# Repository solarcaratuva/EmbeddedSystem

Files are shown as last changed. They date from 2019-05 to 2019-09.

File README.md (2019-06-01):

# UVA Solar Car Team Electrical Team - Embedded System Subgroup
The embedded system sub-group focuses on developing the embedded system for the solar car that controls the CAN bus, driver interface and BPS (Battery Management System). This repository contains all of the design files necessary to implement the electrical control systems necessary for the Solar Car project.

## ECU
The ECU is the primary controller for the majority of systems, including motor control, battery monitoring, driver interface, and MPPT interface. The PCB contains circuitry for interfacing buttons and switches on driver interface, high-current lights and horn, as well as

**!important!**
Not all pins are 12V or even 5V compatible. Certain pins connect directly to the teensy with no protection.

* signal: name of IO signal in Eeschema (may or may not also be the net name)
* voltage: the voltages the pin is designed for
* direction: The direction of the signal relative to the ECU
* description: description of the signal

### User interface input (control)
These pins are used for allowing the driver to command the vehicle. All but the UART pins are 12V logic. To reduce the number of pins required on the MCU, we chose to wire 3 way position switches such that the end contacts connect to the rails and the center contact floats with a resistor divider to ensure the voltage is approximately VCC/2 when the switch is in the middle position.

| signal | pin  | voltage  | direction | description |
|:---:|:----:|:---:|:---:|:---:|
| BRAKE_CTRL |  20  | 0 - 12V  |  input | brake potentiometer, used to implement regen |
| REGEN_CTRL |  17  | 0 - 12V  |  input | regen potentiometer, used to set max regen percentage |
| GEARSHIFT_CTRL  |  14  | 0 - 12V  |  input | 3 way position switch. 12V = forward, 6V = neutral, 0V = reverse |
| TURNSIG_CTRL |  15  | 0 - 12V  |  input | 3 way position switch. 12V = forward, 6V = neutral, 0V = reverse |
| THROTTLE_CTRL |  16  | 0 - 12V  |  input | throttle potentiometer, the gas petal |
| STEER_CTRL |21(A7)| 0 - 12V  |  input | potentiometer on steering wheel, may be used for differential throttle control |
| HAZARD_CTRL |  16  | 0 - 12V  |  input | pushbutton used to activate hazard lights, toggles on changing edge  |
| HORN_CTRL |22(A6)| 0 - 12V  |  input | horn button |
| DOWN_CTRL |  26  | 0 - 12V  |  input | GUI navigation pushbutton |
| UP_CTRL |  27  | 0 - 12V  |  input | GUI navigation pushbutton |
| SEL_CTRL |  28  | 0 - 12V  |  input | GUI navigation pushbutton |
| KILL_SENSE | 2  | 0 - 12V  |  input | used to detect if the power engaging the relays has been cut |
| HAZARD_LED |  25  | 0 - 12V  |  output | connected to hazard button LED |
| UART_1_RX | 0  | 0 - 3.3V |  input | used for Nextion 3.2" LCD |
| UART_1_TX | 1  | 0 - 3.3V |  output | used for Nextion 3.2" LCD |

### Serial interface IO
These pins are used for communicating with various peripherals, components, and subsystems within the car. CAN0 is reserved for the BMS, while CAN1 is used for all less critical systems. UART pins are for future use.

| signal |  pin | voltage  | direction | description |
|:---:|:---:|:---:|:---:|:---:|
| CAN0_H | | 0 - 5V | CAN high  | connected to CAN0 peripheral on Teensy 3.6 through MCP2562 |
| CAN0_L | | 0 - 5V | CAN low | connected to CAN0 peripheral on Teensy 3.6 through MCP2562 |
| CAN1_H | | 0 - 5V | CAN high  | connected to CAN1 peripheral on Teensy 3.6 through MCP2562 |
| CAN1_L | | 0 - 5V | CAN low | connected to CAN1 peripheral on Teensy 3.6 through MCP2562 |
| UART_3_RX | 7 | 0 - 3.3V |  input | reserved for future use |
| UART_3_TX | 8 | 0 - 3.3V |  output | reserved for future use |
| UART_6_RX | 47 | 0 - 3.3V |  input | reserved for future use |
| UART_6_TX | 48 | 0 - 3.3V |  output | reserved for future use |

### Lights and Horn
These pins are capable of high currents (up to 5A distributed among the 4 outputs)

| signal | pin | voltage  | direction | description |
|:---:|:---:|:---:|:---:|:---:|
| HORN | 57 | 0 - 12V  | output  | high power output for car horn (can only source current) |
| HEADLIGHTS | 42 | 0 - 12V  | output  | high power output for headlights (can only source current) |
| BRAKELIGHTS | 56 | 0 - 12V  | output  | high power output for brakelights (can only source current) |
| STROBE | 6 | 0 - 12V  | output  | high power output for strobelight (can only source current) |
| RIGHT_BLINKERS  | 41 | 0 - 12V  | output  | high power output for right blinkers (can only source current) |
| LEFT_BLINKERS | 40 | 0 - 12V  | output  | high power output for left blinkers (can only source current) |
| HORN_CTRL | 22 | 0 - 12V  | input | high power input for horn |
| HEADLIGHT_CTRL  | 23 | 0 - 12V  | input | high power input for headlights |
| BRAKE_CTRL | 20 | 0 - 12v  | input | analog input for brakes (used for regen) |

### Motor control
The motor can be interfaced via UART, CAN, and GPIO. As of now, we do not have any API or knowledge of how to interface the motor over UART, as it is not documented. However it is possible to decompile the android app and reverse engineer whatever the app implements. For now, we are using CAN to retrieve important parameters from the motor such as voltage, current, RPM, throttle, and error codes. The motor only outputs messages over CAN, and does not interpret them.

The table below holds true for both `MOTOR_R*` and `MOTOR_L*` signals.
NOTE: all node names in the table below are preceded with `MOTOR_R*` and `MOTOR_L*`!

| signal | pin (L) | pin (R) |  voltage | direction | description |
|:---:|:---|:---:|:---:|:---:|:---:|
| REGEN_EN | 50 | 53 | 0 - 12V  | output  | enables regenerative braking on motor controller |
| REGEN | 36(pwm) | 37(pwm) | 0 - 5V | output  | analog output sets regen level when throttle is disabled (????) |
| THROTTLE | 35(pwm) | 38(pwm) | 0 - 5V | output  | sets throttle when FWD_EN or REV_EN are enabled. |
| ECO_EN | 49 | 39 | 0 - 12V  | output  | Reduces maximum power of motor controller |
| METER | A11 | A10 | 0 - 12V  | input | analog output from motor controller (????) |
| FWD_EN | 55 | 52 | 0 - 12V  | output  | forward enable |
| REV_EN | 54 | 51 | 0 - 12V  | output  | reverse enable |

## Software
At the moment we have bits and pieces of code written but no unified project as of yet. The CAN repository contains experemantal code for interfacing the CAN peripherals on the Teensy as well as development towards a motor driver. The completed motor driver will eventually be refactored into this repo.

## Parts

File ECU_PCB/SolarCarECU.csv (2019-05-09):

Id | Designator | Package | Quantity | Designation | Supplier and ref
1 | C41,C39,C21,C30,C35,C37,C38,C40 | C_0603_1608Metric | 8 | C
2 | R58,R59,R12,R13,R18,R19,R28,R29,R30,R31,R40,R41,R44,R45,R46,R47 | R_0603_1608Metric | 16 | R
3 | D6,D10,D9,D7,D5,D4,D8,D3 | D_SOD-123 | 8 | D
4 | U1 | Teensy35_36 | 1 | Teensy3.6
5 | R43 | R_1206_3216Metric | 1 | 0
6 | R53,R38,R52,R6,R32,R33,R34,R35,R36,R37,R39 | R_0603_1608Metric | 11 | 1k
7 | U4 | PT78NR112H | 1 | L7805
8 | C28,C26,C27,C29 | C_0603_1608Metric | 4 | 6.8n
9 | U8,U7,U9 | SOIC-16_3.9x9.9mm_P1.27mm | 3 | 4504
10 | BT1 | BatteryHolder_Keystone_1060_1x2032 | 1 | Battery_Cell
11 | J2 | USB_B_OST_USB-B1HSxx_Horizontal | 1 | USB_B
12 | R54,R55,R56,R57,R5,R42 | R_0603_1608Metric | 6 | 47
13 | C3,C2,C11,C12,C13,C14,C15,C16,C17,C36 | C_0603_1608Metric | 10 | 0.47u
14 | C8,C7 | C_0603_1608Metric | 2 | 47u
15 | R48,R49,R50,R51 | R_0603_1608Metric | 4 | 4.7
16 | U10 | SOIC-14_3.9x8.7mm_P1.27mm | 1 | LM324A
17 | C1,C4 | CP_Radial_D13.0mm_P5.00mm | 2 | 470uF
18 | C5,C6,C18,C19,C20 | C_0603_1608Metric | 5 | 4.7u
19 | C9 | C_0603_1608Metric | 1 | 10uF
20 | C10 | CP_Radial_D13.0mm_P5.00mm | 1 | 10uF
21 | C22,C23,C24,C25 | C_0603_1608Metric | 4 | 3.3n
22 | C31,C32,C33,C34 | C_0603_1608Metric | 4 | 2.2n
23 | J4,J5 | PinSocket_1x08_P2.54mm_Vertical | 2 | Screw_Terminal_01x08
24 | J6,J7 | PinSocket_1x14_P2.54mm_Vertical | 2 | Screw_Terminal_01x14
25 | Q1,Q3,Q4,Q5,Q6 | TO-252-2 | 5 | QM6015D
26 | Q2 | SOT-223 | 1 | PZT2222A
27 | R1,R2,R3,R4 | R_0603_1608Metric | 4 | 0
28 | R7,R10,R11 | R_0603_1608Metric | 3 | 120
29 | R8,R9 | R_0603_1608Metric | 2 | 100k
30 | R14,R15,R16,R17 | R_0603_1608Metric | 4 | 8.2k
31 | R20,R21,R22,R23 | R_0603_1608Metric | 4 | 120k
32 | R24,R25,R26,R27 | R_0603_1608Metric | 4 | 36k
33 | U2,U3 | DIP-8_W7.62mm | 2 | EL7202CN
34 | U5,U6 | DIP-8_W7.62mm | 2 | MCP2562-E-P
35 | J1 | PhoenixContact_MCV_1,5_2-G-5.08_1x02_P5.08mm_Vertical | 1 | Screw_Terminal_01x02
36 | J3 | PhoenixContact_MCV_1,5_5-G-5.08_1x05_P5.08mm_Vertical | 1 | Screw_Terminal_01x05
37 | D1 | D_SOD-123 | 1 | D_Schottky
38 | D2 | D_SOD-123 | 1 | D_Zener
39 | G*** | SOLAR | 1 | LOGO
40 | G*** | PowerMax | 1 | LOGO
41 | G*** | WZ | 1 | LOGO
42 | G*** | CJR | 1 | LOGO
43 | G*** | JohnC | 1 | LOGO

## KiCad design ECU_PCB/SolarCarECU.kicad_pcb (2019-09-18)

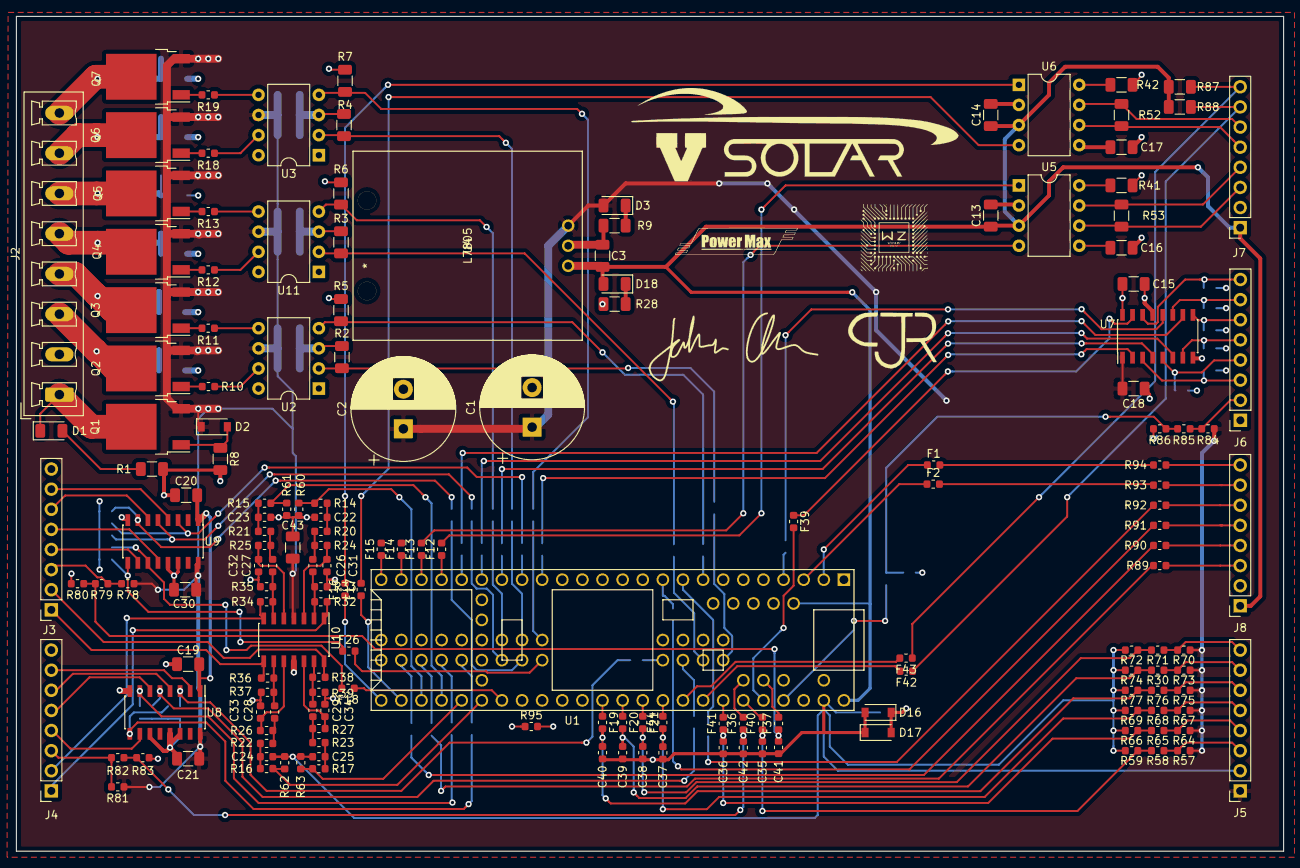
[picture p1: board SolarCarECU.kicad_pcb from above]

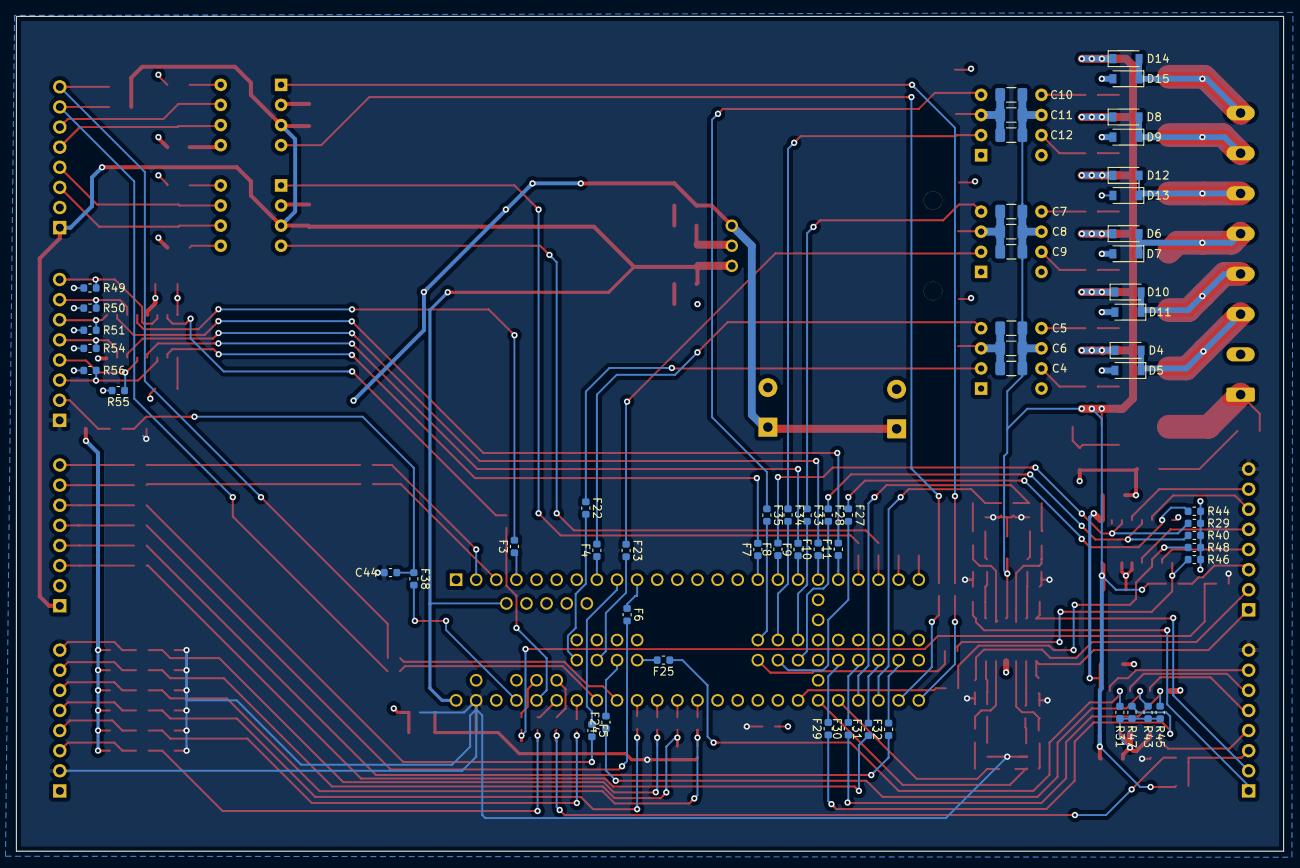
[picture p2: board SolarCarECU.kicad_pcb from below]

Board: 4 copper layers, 160.0 x 105.4 mm, 226 parts (60 on the bottom side), 173 nets.

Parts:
C1, C2: 470uF; CP_Radial_D13.0mm_P5.00mm
C3: 10uF; C_1206_3216Metric
C4, C7, C10, C13, C14, C15, C16, C17, C19, C20, C43: 100n; C_1206_3216Metric
C5, C8, C11, C18, C21, C30: 4.7u; C_1206_3216Metric
C6, C9, C12: 47u; C_1206_3216Metric
C22, C23, C24, C25: 3.3n; C_0603_1608Metric
C26, C27, C28, C29: 6.8n; C_0603_1608Metric
C31, C32, C33, C34: 2.2n; C_0603_1608Metric
C35, C36, C37, C38, C39, C40, C41, C42, C44: 1n; C_0603_1608Metric
D1: 599-0210; LED_1206_3216Metric
D2: D_Zener; D_SOD-123
D3: 599-0230; LED_1206_3216Metric
D4, D5, D6, D7, D8, D9, D10, D11, D12, D13, D14, D15, D16, D17: D; D_SOD-123
D18: 599-0291; LED_1206_3216Metric
F1, F2, F3, F4, F5, F6, F7, F8, F9, F10, F11, F12, F13, F14, F15, F16, F17, F18, F19, F20, F21, F22, F23, F24, F25, F26, F27, F28, F29, F30, F31, F32, F33, F34, F35, F36, F37, F38, F39, F40, F41, F42, F43, F44: Polyfuse; Fuse_0603_1608Metric
J2: Screw_Terminal_01x08; PhoenixContact_MCV_1,5_8-G-5.08_1x08_P5.08mm_Vertical
J3, J4, J5, J6, J7, J8: Screw_Terminal_01x08; PinSocket_1x08_P2.54mm_Vertical
Q1, Q2, Q3, Q4, Q5, Q6, Q7: QM6015D; TO-252-2
R1, R8, R9, R28, R87, R88: 1k; R_1206_3216Metric
R2, R3, R4, R5, R6, R7, R41, R42: 100k; R_1206_3216Metric
R10, R11, R12, R13, R18, R19: 4.7; R_0603_1608Metric
R14, R15, R16, R17: 8.2k; R_0603_1608Metric
R20, R21, R22, R23: 120k; R_0603_1608Metric
R24, R25, R26, R27: 36k; R_0603_1608Metric
R29, R31, R40, R43, R44, R45, R46, R47, R48, R49, R50, R51, R54, R55, R56, R60, R61, R62, R63: 100k; R_0603_1608Metric
R30, R57, R58, R64, R65, R67, R68, R70, R71, R73, R75, R76, R78, R79, R81, R82, R84, R85: 1M; R_0603_1608Metric
R32, R33, R34, R35, R36, R37, R38, R39: 1k; R_0603_1608Metric
R52, R53: 120; R_1206_3216Metric
R59, R66, R69, R72, R74, R77, R80, R83, R86: 330k; R_0603_1608Metric
R89, R90, R91, R92, R93, R94: 47; R_0603_1608Metric
R95: 0; R_0603_1608Metric
U1: Teensy3.6; Teensy35_36
U2, U3, U11: MCP1403; DIP-8_W7.62mm
U4: L7805; PT78NR112H
U5, U6: MCP2562-E-P; DIP-8_W7.62mm
U7, U8, U9: 4504; SOIC-16_3.9x9.9mm_P1.27mm
U10: LM324A; SOIC-14_3.9x8.7mm_P1.27mm

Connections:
+3V3: C15.1, C16.1, C17.1, C19.1, C20.1, U1.15, U1.26, U1.51, U1.75, U5.5, U6.5, U7.16, U8.1, U9.1
+5V: C3.1, C13.1, C14.1, D18.2, J7.1, J8.1, R87.1, R88.1, U1.53, U1.58, U4.3, U5.3, U6.3
+12V: C1.1, C2.1, C4.2, C5.2, C6.2, C7.2, C8.2, C9.2, C10.2, C11.2, C12.2, C18.2, C21.2, C30.2, C43.2, D2.1, D3.2, D4.1, D6.1, D8.1, D10.1, D12.1, D14.1, J5.1, Q1.3, Q2.3, Q3.3, Q4.3, Q5.3, Q6.3, Q7.3, R57.1, R64.1, R67.1, R70.1, R73.1, R75.1, R78.1, R81.1, R84.1, U2.6, U3.6, U4.1, U7.1, U8.16, U9.16, U10.4, U11.6
+VDC: D1.1, J2.1, Q1.2
/BRAKELIGHTS: D6.2, D7.1, J2.5, Q4.2
/BRAKE_CTRL: J5.4, R64.2, R65.1
/CAN0_H: J7.4, R53.1, U5.7
/CAN0_L: J7.3, R53.2, U5.6
/CAN0_RX: F13.2, U5.4
/CAN0_TX: F12.2, U5.1
/CAN1_H: J7.6, R52.1, U6.7
/CAN1_L: J7.5, R52.2, U6.6
/CAN1_RX: F17.2, U6.4
/CAN1_TX: F16.2, U6.1
/DOWN_CTRL: J6.4, R55.1, U7.5
/GEARSHIFT_CTRL: J5.6, R75.2, R76.1
/HAZARD_CTRL: J6.3, R56.1, U7.3
/HEADLIGHTS: D12.2, D13.1, J2.6, Q5.2
/HEADLIGHT_CTRL: J6.2, R84.2, R85.1
/HORN: D4.2, D5.1, J2.3, Q2.2
/HORN_CTRL: J6.8, R49.1, U7.14
/KILL_SENSE: J6.7, R50.1, U7.11
/LEFT_BLINKERS: D14.2, D15.1, J2.8, Q7.2
/LV_BRAKELIGHTS: F23.1, R3.1, U11.2
/LV_BRAKE_CTRL: C36.1, F41.1, R65.2, R66.1
/LV_DOWN_CTRL: F9.2, U7.4
/LV_GEARSHIFT_CTRL: C40.1, F19.2, R76.2, R77.1
/LV_HAZARD_CTRL: F7.2, U7.2
/LV_HAZARD_LED: F8.2, R29.1, U9.3
/LV_HEADLIGHTS: F33.1, R6.1, U11.4
/LV_HEADLIGHT_CTRL: C44.1, F38.1, R85.2, R86.1
/LV_HORN: F22.1, R2.1, U2.2
/LV_HORN_CTRL: F39.1, U7.15
/LV_KILL_SENSE: F3.2, U7.12
/LV_LEFT_BLINKERS: F35.1, R7.1, U3.4
/LV_MOTOR_L_ECO_EN: F30.1, R45.1, U8.7
/LV_MOTOR_L_FWD_EN: F24.1, R43.1, U8.5
/LV_MOTOR_L_METER: C42.1, F36.1, R82.2, R83.1
/LV_MOTOR_L_REGEN_EN: F29.1, R47.1, U8.9
/LV_MOTOR_L_REV_EN: F25.1, R31.1, U8.3
/LV_MOTOR_R_ECO_EN: F18.2, R48.1, U9.11
/LV_MOTOR_R_FWD_EN: F27.1, R44.1, U9.7
/LV_MOTOR_R_METER: C41.1, F37.1, R79.2, R80.1
/LV_MOTOR_R_REGEN_EN: F26.1, R46.1, U9.9
/LV_MOTOR_R_REV_EN: F28.1, R40.1, U9.5
/LV_REGEN_CTRL: C37.1, F44.1, R68.2, R69.1
/LV_RIGHT_BLINKERS: F34.1, R4.1, U3.2
/LV_SEL_CTRL: F11.2, U7.10
/LV_STEER_CTRL: C35.1, F40.1, R58.2, R59.1
/LV_STROBE: F4.2, R5.1, U2.4
/LV_THROTTLE_CTRL: C38.1, F21.2, R71.2, R72.1
/LV_TURNSIG_CTRL: C39.1, F20.2, R30.2, R74.1
/LV_UP_CTRL: F10.2, U7.6
/MOTOR_L_ECO_EN: J4.5, U8.6
/MOTOR_L_FWD_EN: J4.6, U8.4
/MOTOR_L_METER: J4.3, R81.2, R82.1
/MOTOR_L_REGEN: J4.2, R34.1, U10.7
/MOTOR_L_REGEN_EN: J4.4, U8.10
/MOTOR_L_REV_EN: J4.7, U8.2
/MOTOR_L_THROTTLE: J4.1, R32.1, U10.1
/MOTOR_R_ECO_EN: J3.5, U9.12
/MOTOR_R_FWD_EN: J3.6, U9.6
/MOTOR_R_METER: J3.3, R78.2, R79.1
/MOTOR_R_REGEN: J3.2, R38.1, U10.14
/MOTOR_R_REGEN_EN: J3.4, U9.10
/MOTOR_R_REV_EN: J3.7, U9.4
/MOTOR_R_THROTTLE: J3.1, R36.1, U10.8
/PWM_MOTOR_L_REGEN: R15.2, R61.1, U1.33
/PWM_MOTOR_L_THROTTLE: R14.2, R60.1, U1.32
/PWM_MOTOR_R_REGEN: R17.2, R63.1, U1.34
/PWM_MOTOR_R_THROTTLE: R16.2, R62.1, U1.35
/REGEN_CTRL: J5.5, R67.2, R68.1
/RIGHT_BLINKERS: D8.2, D9.1, J2.7, Q6.2
/SCL_0: F42.1, J7.7, R88.2
/SDA_0: F43.1, J7.8, R87.2
/SEL_CTRL: J6.6, R51.1, U7.9
/STEER_CTRL: J5.3, R57.2, R58.1
/STROBE: D10.2, D11.1, J2.4, Q3.2
/THROTTLE_CTRL: J5.8, R70.2, R71.1
/TURNSIG_CTRL: J5.7, R30.1, R73.2
/UART_1_RX: F1.2, R94.2
/UART_1_TX: F2.2, R93.2
/UART_3_RX: F5.2, R92.2
/UART_3_TX: F6.2, R91.2
/UART_6_RX: F32.1, R90.2
/UART_6_TX: F31.1, R89.2
/UP_CTRL: J6.5, R54.1, U7.7
GND: C1.2, C2.2, C3.2, C4.1, C5.1, C6.1, C7.1, C8.1, C9.1, C10.1, C11.1, C12.1, C13.2, C14.2, C15.2, C16.2, C17.2, C18.1, C19.2, C20.2, C21.1, C30.1, D5.2, D7.2, D9.2, D11.2, D13.2, D15.2, D16.1, D17.2, J2.2, J7.2, J8.2, R1.2, R2.2, R3.2, R4.2, R5.2, R6.2, R7.2, R8.2, R9.2, R28.2, R29.2, R31.2, R40.2, R41.2, R42.2, R43.2, R44.2, R45.2, R46.2, R47.2, R48.2, R49.2, R50.2, R51.2, R54.2, R55.2, R56.2, R95.1, U1.1, U1.27, U1.39, U1.61, U1.62, U1.74, U2.3, U3.3, U4.2, U5.2, U6.2, U7.8, U7.13, U8.8, U8.11, U8.13, U8.14, U9.8, U9.13, U9.14, U10.11, U11.3
GNDA: C22.2, C23.2, C24.2, C25.2, C31.1, C32.1, C33.1, C34.1, C35.2, C36.2, C37.2, C38.2, C39.2, C40.2, C41.2, C42.2, C43.1, C44.2, D16.2, D17.1, J3.8, J4.8, J5.2, J6.1, R33.2, R35.2, R37.2, R39.2, R59.2, R60.2, R61.2, R62.2, R63.2, R66.2, R69.2, R72.2, R74.2, R77.2, R80.2, R83.2, R86.2, R95.2, U1.52
unnamed: C22.1, R14.1, R20.2
unnamed: C23.1, R15.1, R21.2
unnamed: C24.1, R16.1, R22.2
unnamed: C25.1, R17.1, R23.2
unnamed: C26.1, R20.1, R24.2
unnamed: C26.2, R32.2, R33.1, U10.2
unnamed: C27.1, R21.1, R25.2
unnamed: C27.2, R34.2, R35.1, U10.6
unnamed: C28.1, R22.1, R26.2
unnamed: C28.2, R36.2, R37.1, U10.9
unnamed: C29.1, R23.1, R27.2
unnamed: C29.2, R38.2, R39.1, U10.13
unnamed: C31.2, R24.1, U10.3
unnamed: C32.2, R25.1, U10.5
unnamed: C33.2, R26.1, U10.10
unnamed: C34.2, R27.1, U10.12
unnamed: D1.2, R1.1
unnamed: D2.2, Q1.1, R8.1
unnamed: D3.1, R9.1
unnamed: D18.1, R28.1
unnamed: F1.1, U1.2
unnamed: F2.1, U1.3
unnamed: F3.1, U1.4
unnamed: F4.1, U1.8
unnamed: F5.1, U1.9
unnamed: F6.1, U1.10
unnamed: F7.1, U1.16
unnamed: F8.1, U1.17
unnamed: F9.1, U1.18
unnamed: F10.1, U1.19
unnamed: F11.1, U1.20
unnamed: F12.1, U1.21
unnamed: F13.1, U1.22
unnamed: F14.1, U1.23
unnamed: F15.1, U1.24
unnamed: F16.1, U1.30
unnamed: F17.1, U1.31
unnamed: F18.1, U1.36
unnamed: F19.1, U1.41
unnamed: F20.1, U1.42
unnamed: F21.1, U1.43
unnamed: F22.2, U1.86
unnamed: F23.2, U1.85
unnamed: F24.2, U1.84
unnamed: F25.2, U1.83
unnamed: F26.2, U1.82
unnamed: F27.2, U1.81
unnamed: F28.2, U1.80
unnamed: F29.2, U1.79
unnamed: F30.2, U1.78
unnamed: F31.2, U1.77
unnamed: F32.2, U1.76
unnamed: F33.2, U1.69
unnamed: F34.2, U1.68
unnamed: F35.2, U1.67
unnamed: F36.2, U1.57
unnamed: F37.2, U1.56
unnamed: F38.2, U1.50
unnamed: F39.2, U1.49
unnamed: F40.2, U1.48
unnamed: F41.2, U1.47
unnamed: F42.2, U1.46
unnamed: F43.2, U1.45
unnamed: F44.2, U1.44
unnamed: J8.3, R89.1
unnamed: J8.4, R90.1
unnamed: J8.5, R91.1
unnamed: J8.6, R92.1
unnamed: J8.7, R93.1
unnamed: J8.8, R94.1
unnamed: Q2.1, R10.1
unnamed: Q3.1, R11.1
unnamed: Q4.1, R12.1
unnamed: Q5.1, R13.1
unnamed: Q6.1, R18.1
unnamed: Q7.1, R19.1
unnamed: R10.2, U2.7
unnamed: R11.2, U2.5
unnamed: R12.2, U11.7
unnamed: R13.2, U11.5
unnamed: R18.2, U3.7
unnamed: R19.2, U3.5
unnamed: R41.1, U5.8
unnamed: R42.1, U6.8

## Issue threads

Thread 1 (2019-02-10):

Add potentiometer on steering rack to allow torque adjustment inner and outer wheel

willzhang05, 2019-02-10:
When turning a corner, the torque on the left and right throttle needs to be adjusted. This can be done with a potentiometer on the steering rack acting as an input.

Closed 2019-03-31.

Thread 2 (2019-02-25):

HORN does not connect to a pin

power-max, 2019-02-25:
There needs to be a connector (a beefy one) for the horn. The Horn is going to be a high-current device (drawing many tens of amps inrush!) so traces need to be short and thick, minimizing loop area to avoid EMI. I think it will fit well near the "lights" connector.

cj-rogers0, 2019-03-05:
Horn Connected

Closed 2019-03-05.

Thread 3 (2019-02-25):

Capacitor/Resistor/Diode packages

power-max, 2019-02-25:
We have purchased a nice 1206 resistor component kit (as the 0603 kit was unavailable), so where space allows, please change the packages to 1206. In areas were layout is dense, (around the op-amp for example) keep the 0603 parts if it makes the layout easier.

I've found a bunch of 0805 capacitors we used for the BatteryTester project awhile back and brought up the more 0805 parts from my capstone, so for decoupling capacitors I think we can use what we have by changing over to 0805.

We need to find a schottky and zener diode for the project. Diodes generally don't come in 0603, least not that I've seen. The schottky diode is just basic reverse polarity protection so anything that has a reasonable low forward Vdrop and can handle 1A should be just fine. Zener diode is used to protect the gate of the MOSFET, and anything between 10V and 25V should be adequate. easy-to-solder SMD package preferred.

cj-rogers0, 2019-03-05:
Diodes changed to a SOD-123 Package

Closed 2019-03-05.

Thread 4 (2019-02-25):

7805 Linear Regulator

power-max, 2019-02-25:
We actually have these nice "7805" drop-in replacement modules up at the reactor in my component drawer. The pinout is the same but they are DC-DC converters and are much larger. A custom footprint (custom courtyard and silkscreen outline) will need to be created to use them. It will help minimize power dissipation within the ECU and improve efficiency.

cj-rogers0, 2019-03-05:
Footprint Found

Closed 2019-03-05.

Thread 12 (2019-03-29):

Check all transistors for correct pinout

power-max, 2019-03-29:

Closed 2019-04-27.

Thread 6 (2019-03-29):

Reverse CANH and CANL on PCB connectors to improve rounting

power-max, 2019-03-29:

Closed 2019-03-31.

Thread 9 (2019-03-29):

Add flyback protection diode or RCD snubber to Q6,Q5,Q4, and especially Q3

power-max, 2019-03-29:

power-max, 2019-03-31:
fixed in next commit

Closed 2019-03-31.

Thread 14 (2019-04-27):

Issues with PCB

john-chrosniak, 2019-04-27:
Need separate pins for left and right turn signals
LM324 needs 12 V supply

Closed 2019-04-28.

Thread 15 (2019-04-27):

replace 14 inch connector

power-max, 2019-04-27:

Closed 2019-04-28.

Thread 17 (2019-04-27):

14 position screw terminals are too long. Not acquirable.

arslan-aziz, 2019-04-27:
12 position terminals are the max length we can find at $3 a piece.

arslan-aziz, 2019-04-27:
We can remove the following pins from the 14 pin connectors
-UART (three extra is too future-proof)
-UP_CTRL
-DOWN_CTRL
-SEL_CTRL
-GEARSHIFT_CTRL
-

Closed 2019-04-28.

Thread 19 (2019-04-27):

fix documentation

power-max, 2019-04-27:
pin mapping needs updating

power-max, 2019-04-28:
many pins have been changed but README is not up to date with changes.

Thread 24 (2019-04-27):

Not an issue, just saying hi

arslan-aziz, 2019-04-27:

power-max, 2019-04-28:
Hi!

Closed 2019-05-14.

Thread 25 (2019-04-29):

Issue with Teensy Pins

john-chrosniak, 2019-04-29:
- Need a pin to read the state of the horn button (digital)
- Don't need a pin for the hazard_leds, as the lights in use are just the turn signals and the brakelights
- Need a pin to read the state of the daytime running lights switch (digital)

Closed 2019-04-30.

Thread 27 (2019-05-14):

+12V is shorted to ground on pin 1 of J6

willzhang05, 2019-05-14:
currently traces need to be cut in order for the board to work

power-max, 2019-05-14:
I have already fixed this. Pull the latest KiCad to see if the fix was implemented.

power-max, 2019-06-02:
Fixed as of PCBv3

Closed 2019-06-02.

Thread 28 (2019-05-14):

+12V input and ground should be on its own screw terminal or barrel jack

willzhang05, 2019-05-14:

power-max, 2019-05-14:
I was limited in space so the compromise I made was to have a shared ground point and a 12V in observed on the PCB and schematic.

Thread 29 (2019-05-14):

Need an output pin for HAZARD_LED

willzhang05, 2019-05-14:
There's currently no output pin for HAZARD_LED

power-max, 2019-05-14:
HAZARD_LED is depricated. Needs to be added (or removed, actually) from the documentation.

Closed 2019-06-02.

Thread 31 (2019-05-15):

J6 is sitting on top of voltage divider resistors

arslan-aziz, 2019-05-15:

power-max, 2019-06-02:
Not sure exactly what the issue is here. Resistors on the top layer close to the screw terminals were pushed back.

Closed 2019-06-02.

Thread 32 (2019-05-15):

no pin for strobe output on Teensy

arslan-aziz, 2019-05-15:

power-max, 2019-06-02:
Fixed as of PCBv3

Closed 2019-06-02.

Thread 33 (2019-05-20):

Decoupling capacitors C12,C9,C6 (47 uF) are 1210 package. Need more space around pads. Too difficult to solder

arslan-aziz, 2019-05-20:

power-max, 2019-06-02:
Or lets just not solder 1210 components there. 47uF is a bit excessive, although they can be bodged on if needed.

Closed 2019-06-02.

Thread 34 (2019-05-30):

pulldown/pullup resistors should be added to all teensy output pins

power-max, 2019-05-30:
All teensy output pins are high impedance during the booting sequence. This may result in spurious signals resulting in no control over throttle, lights, horn, etc. when the car is first turned on. Resistors should be added as pulldown or pullups to ensure an always known state during bootup.

workaround: power-sequencing. Power the PCB several seconds before applying power to any other system.

power-max, 2019-06-02:
Fixed as of PCBv3

Closed 2019-06-02.

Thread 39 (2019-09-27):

Find a suitable replacement or better footprint solution for LM7805

willzhang05, 2019-09-27:

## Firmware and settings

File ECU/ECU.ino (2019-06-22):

#include <ArduinoJson.h>
#include "BPS.h"
#include "KLS.h"
//#include "UI.h"
#include "console.h"
#include "lights.h"
#include "pindef.h"

// used strictly for BMS
FlexCAN Can0(500000, 0);
// wired to both motor controllers.
FlexCAN Can1(250000, 1);

// 2 CAN structs to store received data
CAN_message_t msg[2];

BPS bps;
// Left motor initialized with source address 0x05
KLS kls_l(0x05);
// Right motor initialized with source address 0x06
KLS kls_r(0x06);

// UI lcd;

char cmd = 'X';
char buf = 'X';

void setup() {
    Serial.begin(115200);

    digitalWrite(PIN_BRAKE_CTRL, LOW);
    pinMode(PIN_BRAKE_CTRL, INPUT);
    digitalWrite(PIN_REGEN_CTRL, LOW);
    pinMode(PIN_REGEN_CTRL, INPUT);
    digitalWrite(PIN_GEARSHIFT_CTRL, LOW);
    pinMode(PIN_GEARSHIFT_CTRL, INPUT);
    digitalWrite(PIN_TURNSIG_CTRL, LOW);
    pinMode(PIN_TURNSIG_CTRL, INPUT);
    digitalWrite(PIN_THROTTLE_CTRL, LOW);
    pinMode(PIN_THROTTLE_CTRL, INPUT);
    digitalWrite(PIN_STEER_CTRL, LOW);
    pinMode(PIN_STEER_CTRL, INPUT);
    digitalWrite(PIN_HAZARD_CTRL, LOW);
    pinMode(PIN_HAZARD_CTRL, INPUT);
    attachInterrupt(digitalPinToInterrupt(PIN_HAZARD_CTRL), toggle_hazard_state, RISING);
    digitalWrite(PIN_DOWN_CTRL, LOW);
    pinMode(PIN_DOWN_CTRL, INPUT);
    digitalWrite(PIN_UP_CTRL, LOW);
    pinMode(PIN_UP_CTRL, INPUT);
    digitalWrite(PIN_SEL_CTRL, LOW);
    pinMode(PIN_SEL_CTRL, INPUT);
    digitalWrite(PIN_KILL_SENSE, LOW);
    pinMode(PIN_KILL_SENSE, INPUT);
    digitalWrite(PIN_HAZARD_LED, LOW);
    pinMode(PIN_HAZARD_LED, INPUT);
    digitalWrite(PIN_UART_1_RX, LOW);
    pinMode(PIN_UART_1_RX, INPUT);
    digitalWrite(PIN_UART_1_TX, LOW);
    pinMode(PIN_UART_1_TX, INPUT);

    /******************************************/
    /* pin definitions for motor controllers  */
    /******************************************/
    digitalWrite(PIN_MOTOR_L_REGEN_EN, LOW);
    pinMode(PIN_MOTOR_L_REGEN_EN, OUTPUT);
    digitalWrite(PIN_MOTOR_L_REGEN, LOW);
    pinMode(PIN_MOTOR_L_REGEN, OUTPUT);
    digitalWrite(PIN_MOTOR_L_THROTTLE, LOW);
    pinMode(PIN_MOTOR_L_THROTTLE, OUTPUT);
    digitalWrite(PIN_MOTOR_L_ECO_EN, LOW);
    pinMode(PIN_MOTOR_L_ECO_EN, OUTPUT);
    digitalWrite(PIN_MOTOR_L_METER, LOW);
    pinMode(PIN_MOTOR_L_METER, OUTPUT);
    digitalWrite(PIN_MOTOR_L_FWD_EN, LOW);
    pinMode(PIN_MOTOR_L_FWD_EN, OUTPUT);
    digitalWrite(PIN_MOTOR_L_REV_EN, LOW);
    pinMode(PIN_MOTOR_L_REV_EN, OUTPUT);

    digitalWrite(PIN_MOTOR_R_REGEN_EN, LOW);
    pinMode(PIN_MOTOR_R_REGEN_EN, OUTPUT);
    digitalWrite(PIN_MOTOR_R_REGEN, LOW);
    pinMode(PIN_MOTOR_R_REGEN, OUTPUT);
    digitalWrite(PIN_MOTOR_R_THROTTLE, LOW);
    pinMode(PIN_MOTOR_R_THROTTLE, OUTPUT);
    digitalWrite(PIN_MOTOR_R_ECO_EN, LOW);
    pinMode(PIN_MOTOR_R_ECO_EN, OUTPUT);
    digitalWrite(PIN_MOTOR_R_METER, LOW);
    pinMode(PIN_MOTOR_R_METER, OUTPUT);
    digitalWrite(PIN_MOTOR_R_FWD_EN, LOW);
    pinMode(PIN_MOTOR_R_FWD_EN, OUTPUT);
    digitalWrite(PIN_MOTOR_R_REV_EN, LOW);
    pinMode(PIN_MOTOR_R_REV_EN, OUTPUT);

    /******************************************/
    /* pin definitions for high power devices */
    /******************************************/
    digitalWrite(PIN_HORN, LOW);
    pinMode(PIN_HORN, OUTPUT);
    digitalWrite(PIN_HEADLIGHTS, LOW);
    pinMode(PIN_HEADLIGHTS, OUTPUT);
    digitalWrite(PIN_BRAKELIGHTS, LOW);
    pinMode(PIN_BRAKELIGHTS, OUTPUT);
    digitalWrite(PIN_STROBE_CTRL, LOW);
    pinMode(PIN_STROBE_CTRL, OUTPUT);
    digitalWrite(PIN_RIGHT_BLINKERS, LOW);
    pinMode(PIN_RIGHT_BLINKERS, OUTPUT);
    digitalWrite(PIN_LEFT_BLINKERS, LOW);
    pinMode(PIN_LEFT_BLINKERS, OUTPUT);
    digitalWrite(PIN_HEADLIGHT_CTRL, LOW);
    pinMode(PIN_HEADLIGHT_CTRL, INPUT);
    digitalWrite(PIN_HORN_CTRL, LOW);
    pinMode(PIN_HORN_CTRL, INPUT);
    digitalWrite(PIN_BRAKE_CTRL, LOW);
    pinMode(PIN_BRAKE_CTRL, INPUT);

    Can0.begin();
    Can1.begin();
    // UI::init();
}

void loop() {
    // read CANbus busses and provide CAN packet to respective libraries
    if (Can0.available()) {
        Can0.read(msg[0]);
        bps.parse(msg[0]);
    }
    if (Can1.available()) {
        Can1.read(msg[1]);
        kls_l.parse(msg[1]);
        kls_r.parse(msg[1]);
        // Serial.println("---");
        // kls_l.print();
        // kls_r.print();
    }

    // set throttle for motor
    uint32_t throttle = map(analogRead(PIN_THROTTLE_CTRL), 0, 1023, 0, MAX_PWM);

    kls_l.set_throttle(throttle);
    kls_r.set_throttle(throttle);

    switch (analogRead(PIN_GEARSHIFT_CTRL)) {
        case 0 ... 255:
            kls_l.set_direction(FWD);
            kls_r.set_direction(FWD);
            break;
        case 768 ... 1023:
            kls_l.set_direction(REV);
            kls_r.set_direction(REV);
            break;
        default:
            kls_l.set_direction(NEU);
            kls_r.set_direction(NEU);
            kls_l.set_throttle(0);
            kls_r.set_throttle(0);
            break;
    }

    if (Serial.available() > 0) {
        buf = Serial.read();
        if (buf == 'L' || buf == 'R' || buf == 'X') {
            cmd = buf;
        }
    }
    // Serial.println(cmd);

    // control lights and horn
    // Serial.println(analogRead(PIN_TURNSIG_CTRL));
    // uint16_t turnsig_value = analogRead(PIN_TURNSIG_CTRL);
    // switch (turnsig_value) {

    switch (cmd) {
        // case 0 ... 255:
        case 'L':
            turn_state = LEFT;
            break;
        case 'R':
            // case 768 ... 1023:
            turn_state = RIGHT;
            break;
        default:
            turn_state = OFF;
            break;
    }

    headlights_state = digitalRead(PIN_HEADLIGHT_CTRL);
    horn_state = !digitalRead(PIN_HORN_CTRL);
    brakelights_state = !digitalRead(PIN_BRAKE_CTRL);

    turn_signal();
    hazards();
    headlights();
    horn();
    brakelights();

    // LCD UI stuff
    // if (FAULT){
    // UI::fault_condition(char* str); //Only if there is a fault
    //}
    // FUN ONLY IF WANTED (STILL NEED TO BE IMPLEMENTED IN UI.h CURRENTLY DO NOTHING
    // lcd.right_turn_signal_update(bool on);
    // lcd.left_turn_singal_update(bool on);
    /*UI::SOC_update(0);  // TODO: need to convert batt_status->pack_SOC from a float to an int, or
                        // better, change your function to accept float. --maxim
    UI::speed_update((int)(((kls_l.status.rpm * 14) + (kls_r.status.rpm * 14)) / 2));
    UI::bat_voltage_update((int)bps.batt_stat.pack_voltage);
    UI::bat_current_update((int)bps.batt_stat.pack_current);
    UI::bat_temp_update((int)bps.batt_stat.pack_avg_temp);
    UI::regen_level_update(0);  // DO WE HAVE A REGEN LEVEL VAR?? we do now (untested). --maxim.
    */
}

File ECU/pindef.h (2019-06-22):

#ifndef __PINDEF_H__
#define __PINDEF_H__

/******************************************/
/*  pin definitions for driver interface  */
/******************************************/
#define PIN_BRAKE_CTRL 20      // analog input
#define PIN_REGEN_CTRL 17      // analog input
#define PIN_GEARSHIFT_CTRL 14  // analog input
#define PIN_TURNSIG_CTRL A22   // analog input
#define PIN_THROTTLE_CTRL 16   // analog input
#define PIN_STEER_CTRL 21      // analog input
#define PIN_HAZARD_CTRL 24     // binary input (pushbutton switch)
#define PIN_DOWN_CTRL 26       // binary input (pushbutton switch)
#define PIN_UP_CTRL 27         // binary input (pushbutton switch)
#define PIN_SEL_CTRL 28        // analog input (pushbutton switch)
#define PIN_KILL_SENSE 2       // binary input
#define PIN_HAZARD_LED 25
#define PIN_UART_1_RX 0  // used for nextion LCD
#define PIN_UART_1_TX 1  // used for nextion LCD

/******************************************/
/* pin definitions for motor controllers  */
/******************************************/
#define PIN_MOTOR_L_REGEN_EN 50  // binary output
#define PIN_MOTOR_L_REGEN 36     // pwm output (0% - 100%)
#define PIN_MOTOR_L_THROTTLE 35  // pwm output (0% - 100%)
#define PIN_MOTOR_L_ECO_EN 49    // binary output
#define PIN_MOTOR_L_METER A11    // analog input
#define PIN_MOTOR_L_FWD_EN 55    // binary output
#define PIN_MOTOR_L_REV_EN 54    // binary output

#define PIN_MOTOR_R_REGEN_EN 53  // binary output
#define PIN_MOTOR_R_REGEN 37     // pwm output
#define PIN_MOTOR_R_THROTTLE 38  // pwm output
#define PIN_MOTOR_R_ECO_EN 39    // binary output
#define PIN_MOTOR_R_METER A10    // analog input
#define PIN_MOTOR_R_FWD_EN 52    // binary output
#define PIN_MOTOR_R_REV_EN 51    // binary output

/******************************************/
/* pin definitions for high power devices */
/******************************************/
#define PIN_HORN 57            // binary output
#define PIN_HEADLIGHTS 42      // binary output
#define PIN_BRAKELIGHTS 56     // binary output
#define PIN_STROBE_CTRL 6      // output
#define PIN_RIGHT_BLINKERS 41  // binary output
#define PIN_LEFT_BLINKERS 40   // binary output
#define PIN_HEADLIGHT_CTRL 23  // binary input
#define PIN_HORN_CTRL 22       // binary input
#define PIN_BRAKE_CTRL 20      // binary input

#endif  // __PINDEF_H__

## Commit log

2019-02-09 initial commit of Primary ECU circuit and PCB
    [SolarCarECU.kicad_pcb, SolarCarECU.sch]
2019-02-11 added optional CAN termination, added proper MOSFET driver and fixed MOSFET connections for high power devices
    [SolarCarECU.sch]
2019-02-16 Added teensy code for motor controller
    [SolarCarECU.sch]
2019-02-24 Footprints Completed
    [SolarCarECU.sch]
2019-02-25 begun layout of PCB
    [SolarCarECU.kicad_pcb, SolarCarECU.sch]
2019-03-04 Component Layout MC
    MOSFET Driver, Level Shifter, OpAmp
    [SolarCarECU.kicad_pcb, SolarCarECU.sch]
2019-03-10 Motor controller Routing
    GND Vias not completed.
    [SolarCarECU.kicad_pcb, SolarCarECU.sch]
2019-03-23 MC Routing
    [SolarCarECU.kicad_pcb, SolarCarECU.sch]
2019-03-29 Fixed wiring and added resistors
    Changed wiring of mosfet driver vcc from ground to 5V and added resistors between mosfet gates and mosfet drivers
    [SolarCarECU.kicad_pcb, SolarCarECU.sch]
2019-03-29 lots of things
    [SolarCarECU.kicad_pcb, SolarCarECU.sch]
2019-03-30 added logos
    [SolarCarECU.kicad_pcb, SolarCarECU.sch]
2019-03-31 PCB prototype finished, documention added
    [SolarCarECU.kicad_pcb, SolarCarECU.sch]
2019-03-31 fixed UART_1_* pins, added LV_KILL_SENSE, added *STEER_CTRL*
    [SolarCarECU.kicad_pcb, SolarCarECU.sch]
2019-03-31 added STEER_CTRL to documentation
2019-04-01 move BMS into CAN
2019-04-28 reworked PCB and fixed all issues brought up
    [SolarCarECU.kicad_pcb, SolarCarECU.sch]
2019-04-29 added HORN_CTRL and fixed silkscreen issues
    [SolarCarECU.kicad_pcb, SolarCarECU.sch]
2019-04-30 added HEADLIGHT_CTRL pin but had to sacrifice a 12V output for it.
    [SolarCarECU.kicad_pcb, SolarCarECU.sch]
2019-05-09 fixed pin mapping for new PCB
2019-05-09 fixed PCB and schematic
    [SolarCarECU-B.Cu.gbr, SolarCarECU-B.Mask.gbr, SolarCarECU-B.Paste.gbr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]
2019-05-09 schema update
    [SolarCarECU.sch, _saved_SolarCarECU.sch]
2019-05-14 add constant definitions for bps errors
    [bps_err.h]
2019-05-31 pre-alpha, completely untested. Added most of the nessesary code to main except BMS and UI implementation.
2019-05-31 cleanup and fix git modules
    [ECU.ino, KLS.cpp]
2019-05-31 add arduinojson.h and add back call to lights functions
2019-05-31 fix case
2019-06-01 added HORN pin
2019-06-02 now compiles. Fixed UI.h, ECU.ino (UI related code), and added several new functions to KLS.h
    [ECU.ino, KLS.cpp]
2019-06-02 added pulldown resistors to schematic. No PCB edits done.
    [SolarCarECU.sch]
2019-06-02 added resistors to handle floating condition
    [SolarCarECU.sch]
2019-06-03 finished PCB
    [SolarCarECU.sch]
2019-06-03 finished PCB (but forgot to save so commiting again)
    [SolarCarECU.kicad_pcb, SolarCarECU.sch]
2019-06-19 fix throttle code
2019-06-19 remove constants and fix UI.h bugs
    [ECU.ino]
2019-06-19 fix a ton of bugs
    [ECU.ino, KLS.cpp, pindef.h]
2019-06-21 added PTC fuses to all teensy inputs. PCB not modified to match new PCB.
    [SolarCarECU.kicad_pcb, SolarCarECU.sch]
2019-08-28 filled zone to extend over entire edge cuts
    [SolarCarECU.kicad_pcb]
2019-08-28 added fuse footprints, added 0 ohm resistor to keep gnd/gnda labels consistent, need to update netlist in pcbnew
    [SolarCarECU.sch]
2019-08-29 laid tracks for fuses in pcb. bypass capacitors are not clearing rats nest for some reason...is this a problem?
    [SolarCarECU.kicad_pcb, SolarCarECU.sch]
2019-08-30 fix a couple traces
    [SolarCarECU.kicad_pcb]
2019-08-31 fixed drc and routing errors
    [SolarCarECU.kicad_pcb]
2019-09-02 clean up some traces
    [SolarCarECU.kicad_pcb]
2019-09-07 route some traces under 12v plane to reduce resistance per prof. powell
    [SolarCarECU.kicad_pcb]
2019-09-07 thickened up some traces
    [SolarCarECU.kicad_pcb]
2019-09-15 fix 12v islands and added vias that max removed
    [SolarCarECU.kicad_pcb]
2019-09-15 fix weird remnants of 12v traces
    [SolarCarECU.kicad_pcb]

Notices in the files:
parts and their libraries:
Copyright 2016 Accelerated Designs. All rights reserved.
